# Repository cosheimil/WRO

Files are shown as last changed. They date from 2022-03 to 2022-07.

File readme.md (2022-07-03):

WRO logo
# WRO FE 2022
## Задача:
Задача сезона не просто создание беспилотного автомобиля – это гонка на время. На
трассе не будет одновременно нескольких автомобилей. Вместо этого автомобиль за
попытку должен достичь лучшего времени, проехав несколько кругов полностью
автономно. Дорожные знаки указывают сторону полосы движения, по которой должен
следовать автомобиль. Если на пути красный столб – автомобиль должен держаться
правой стороны полосы, если зеленый - левой стороны полосы.
Задание считается выполненным, если автомобиль проехал 3 круга. Запрещено сбивать
или сдвигать с места дорожные знаки.
Направление, в котором автомобиль должен двигаться по трассе (по часовой стрелке
или против часовой стрелки), будет варьироваться в разных матчах. Стартовая позиция
автомобиля, а также количество и расположение дорожных знаков определяются
случайным образом во время жеребьевки перед матчем (после карантинного времени).
Основа робота - камера OpenMV H7 Plus. С помощью ее и micropython на борту возможно отслеживание объектов внутри кадра и управление пинами GPIO. Так как эта камера фактически pyboard, но с камерой. A pyboard это оффициальная плата с GPIO выводами.
Также выполнен шилд расширения для данной платы на микросхеме drv8833 для управления мотором задней оси и стабилизацией питания на 5в для пиатния камеры.
| Фото | Вид |
| :--- | :--- |
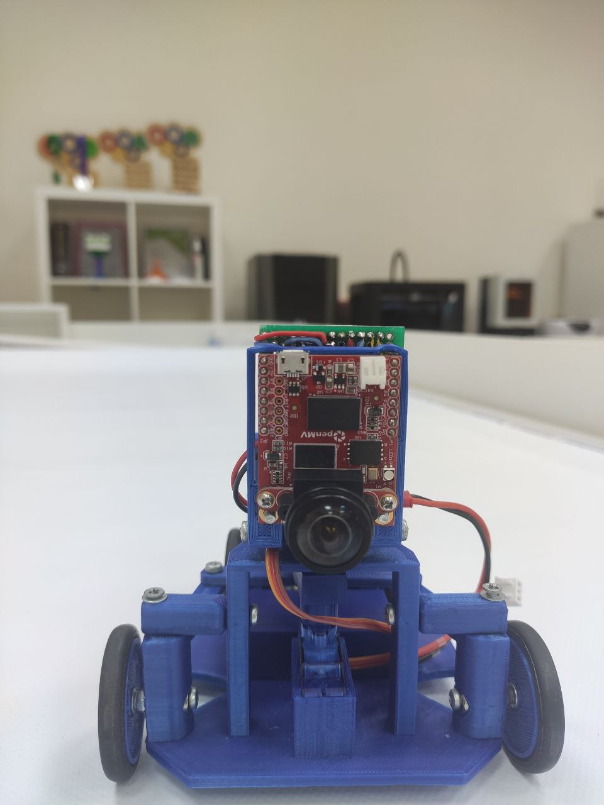
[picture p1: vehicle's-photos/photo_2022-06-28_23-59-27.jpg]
robot1
| | Спереди |
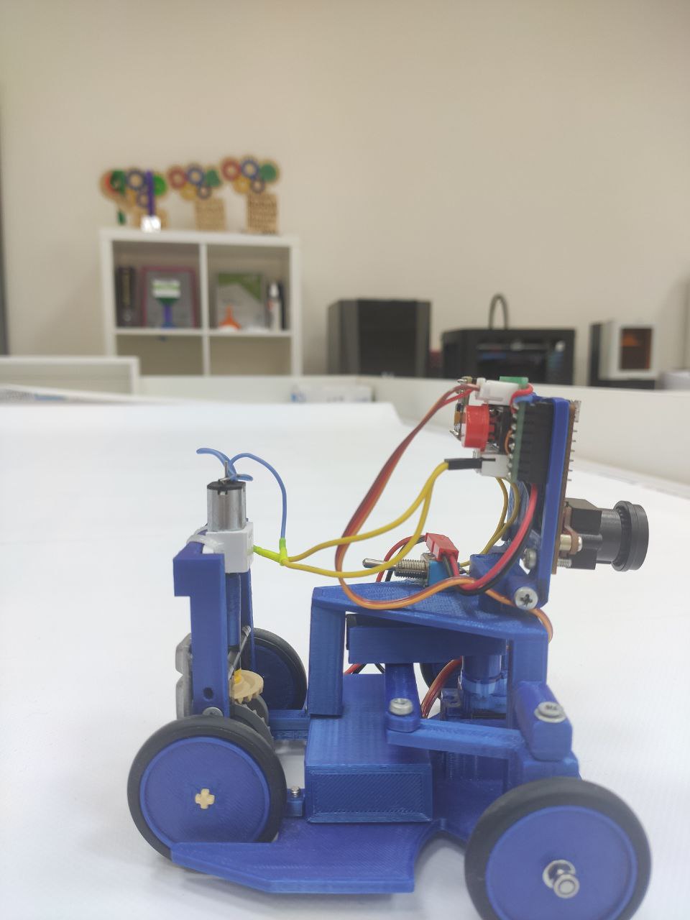
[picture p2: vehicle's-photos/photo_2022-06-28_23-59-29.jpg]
robot2
| | Сбоку |
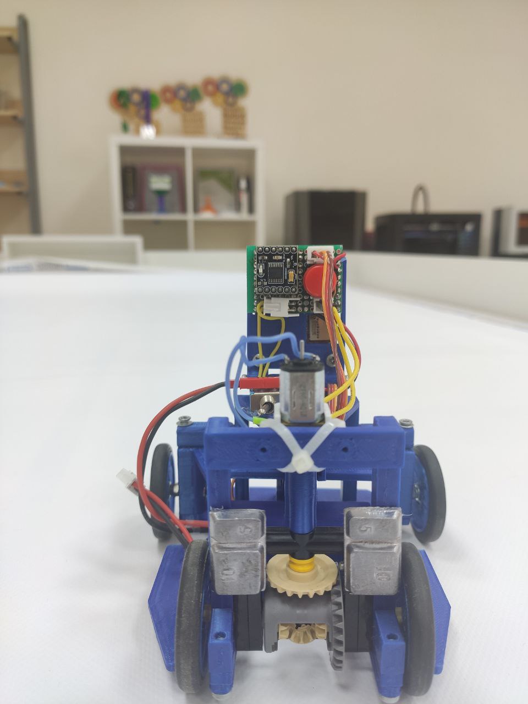
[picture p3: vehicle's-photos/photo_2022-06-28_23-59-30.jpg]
robot3
| | Сзади|
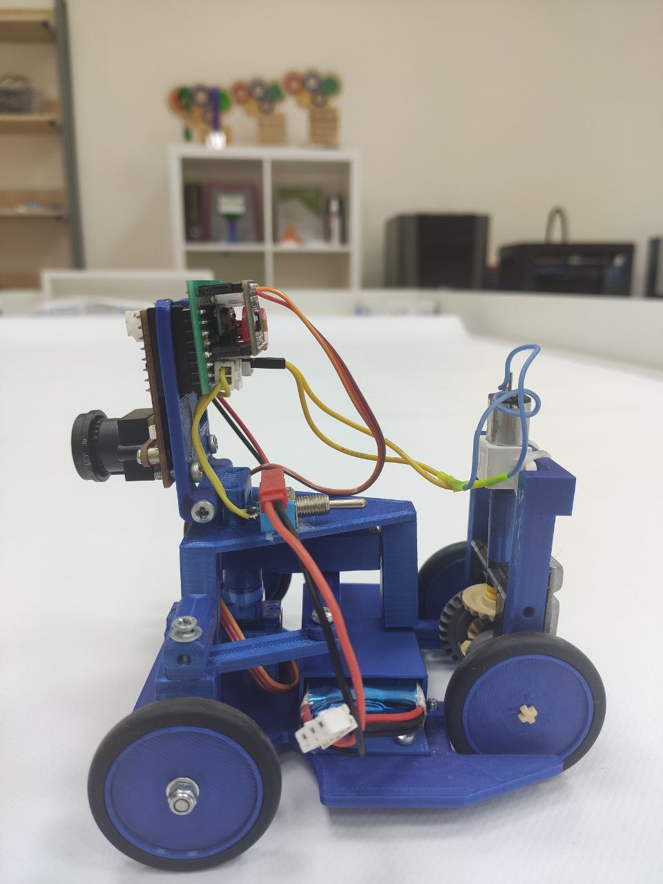
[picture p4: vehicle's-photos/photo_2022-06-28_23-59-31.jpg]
robot4
| | Сбоку|
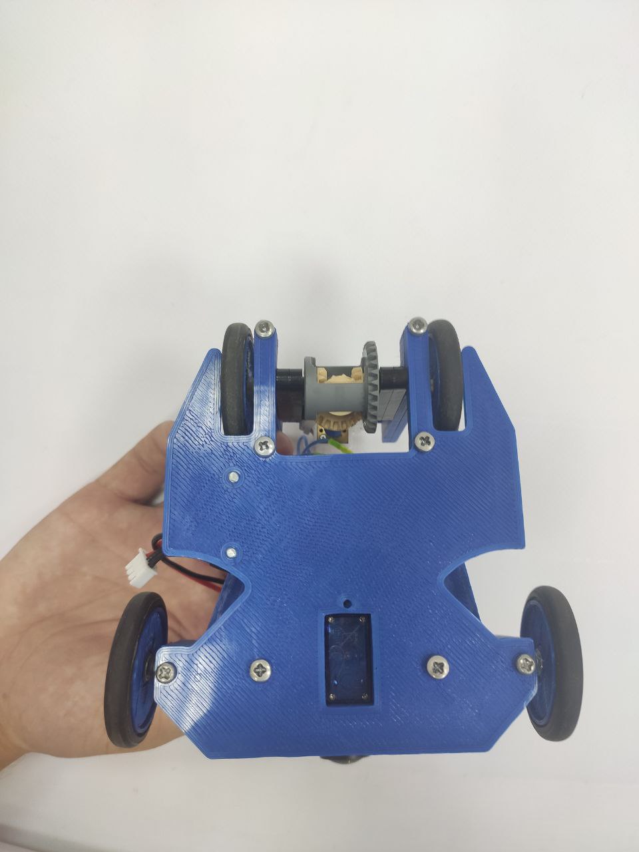
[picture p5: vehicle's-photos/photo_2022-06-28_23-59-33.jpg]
robot5
| | Снизу|
### Конструкция: 
Управление роботом также, как и в настоящей машине: один мотор, передняя ось с соблюдением угла аккермана. Управление передней оси осуществляется с помощью сервопривода MG 90S. А задняя ось приводится в движение с помощью обычного коллекторного мотора с соотношением 150:1 на 6в.
### Реализация конструкции: 
Все части робота были выполнены в CAD Компас 3D V19. в данном CADе присутствуют осовные операции для моделирования и сборка элементов, что идеально подходит для данной задачи.
Все детали напечатаны на 3d-принтере пластиком PLA. Данный пластик идеально подходит для поставленной ранее задачи, так как обладает хорошей прочностью и легким весом.
### Программная часть: 
Камера программируется на MicroPython в среде от производителя - OpenMV IDE. 
В данной среде возможно программировать, отлаживать и загружать код на плату. Также в данной среде поддерживается подсветка синтаксиса и документация к функциям, что делает программирование данной платы очень удобным.

### Алгоритм: 
Алгоритм делится на 3 части:
1) Движение робота до 1 поворота (до первой оранжевой или синей линии на повороте)
2) Движение, если виден кубик
3) Движение при кубике вне кадра

#### 1 
Кадр делится на 2 равные части (разрез по вертикали), определяется кол-во черного в правой и левой. Робот поворачивает в ту сторону, где меньше черного. После того как будет замечена оранжевая или синяя линия (по определенному цветовому диапозону находится прямоугольник некоторого размера) алгоритм переходит ко 2 или 3 части в зависимости от ситуации

#### 2
На некотором расстояние определяется кубик одного из цветов. В зависимости от цвета совершается такой поворот робота (стоит ПИД-регулятор), чтобы центр определенного кубика находился на 20 пикселя от правого (зеленый куб) или от левого (красный куб) края кадра. В таком случае поворот получается достаточно плавным, чтобы не врезаться в куб или стенку

#### 3
Если куба в кадре нет, то робот будет действовать так:
Определяет кол-во черного цвета в правой (если движение против часовой) или в левой (если движение по часовой) половине кадра. Направление движения робота (против часовой или по часовой) определяется по первой увиденной линии на 1 повороте (если оранжевая, то по часовой, если синяя - против часовой). Далее робот с помощью ПИД-регулятора стремится сохранять определенное подобранное кол-во черного в этом секторе.

Тормозит робот после прохождения 12 поворотов (3 круга)

### Процесс сборки
Для сборки робота необходимо напечатать на 3d принтере все компоненты из папки models. И также докупить компоненты [motor](https://www.pololu.com/product/3042), [servo](https://aliexpress.ru/item/1005002235406689.html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,searchweb201602_,searchweb201603_), [motor driver](https://mcustore.ru/store/moduli/drajver-dvigatelya-drv8833/), [OpenMV H7 Plus](https://amperka.ru/product/openmv-cam-h7-plus)
В итоге пакет деталей должен выглядеть примерно так:
- `основа робота`
- `передние кулаки` x2
- `держатели передних кулаков` x2
- `основа камеры`
- `крепление камеры`
- `бампер камеры`
- `батарейный отсек`
- `крепление для дифференциала`
- `колеса` x4
- `вал переходник`
- `OpenMV H7 Plus`
- `сервопривод MG 90S`
- `качалка от сервы`
- `качалка на 3d-принтере`
- `аккамулятор`
- `лего детали`
- `мотор`
- `горстка винтов, гаек и шайб`

1) В основу робота надо вкрутить два передних кулака с использованием шайб m3 и винтов такого же размера
2) В основу необходимо вставить сервопривод и надежно его закрепить внутри самой платформы
3) На сервопривод необходимо одеть качалку с откусанными лепестками и поверх данной конструкции саму качалку, напечатанную на 3d принетере
4) Скрепляется рычаг с кулаки передней оси и продевается в углубление качалки из 3-его шага
5) В основу камеры вкручивается держатель для камеры
6) На камеру одевается бампер
7) Система из шага 6 и 5 скручивается винтами m3 
8) Конструкция из шага 7 вкручивается в основу винтами m3 
9) Батарейный отсек, внутри которой уже заложен аккум, вкручивается в платформу
10) В крепление дифференциала вкручивается сам лего дифференциал
11) Сборка из шага 10 закручивается в платформу
12) На камеру одевается шилд, спаянный по схеме
13) Все провода подключаеются согласно схеме

## Электронные компоненты
#### OpenMV H7 Plus
Мы решили использовать именно эту камеру, так как она обладает хорошим процессором и flash памятью, что позволяет быстрее обрабатывать кадры по сравнению с ее собратьями из данной серии

#### MG 90S
Используется данная серва, потому что алюминиевые шестеренки и алюминиевый вал не дают прокрутится валу и обеспечивает точное позиционирование робота в пространстве

#### pololu motor 6v 150:1
Данный мотор, потому что именно он смог работать адекватно на 7.4v вместо заявленных 6v и не перегреваться

#### преобразователь питания
Использовался китаец под кодовым названием 0j10393, так как за свою цену и размеры он работает идеально

#### DRV8833
Для управления двигателями используется драйвер DRV8833, который позволяет одновременно управлять двумя коллекторными двигателями. Внутри микросхемы драйвера содержится два независимых Н-моста, рассчитанных на напряжение от 2,7 до 10,8 В, с рабочим током каждого канала до 0,5 А без радиатора или до 1,5 А с радиатором, установленным на микросхеме.

## Content
- `models` в этой папке хранятся все файлы робота, напечатанные на 3d-принтере. Все файлы моделей робота, не включая конечную сборку.
- `schemes` содержит принципиальные схемы робота
- `src` вся програмная часть
- `team-photos` фото команды (оффициальное и в процессе работы)
- `vehicle's-photos` фото робота (с разных видов)

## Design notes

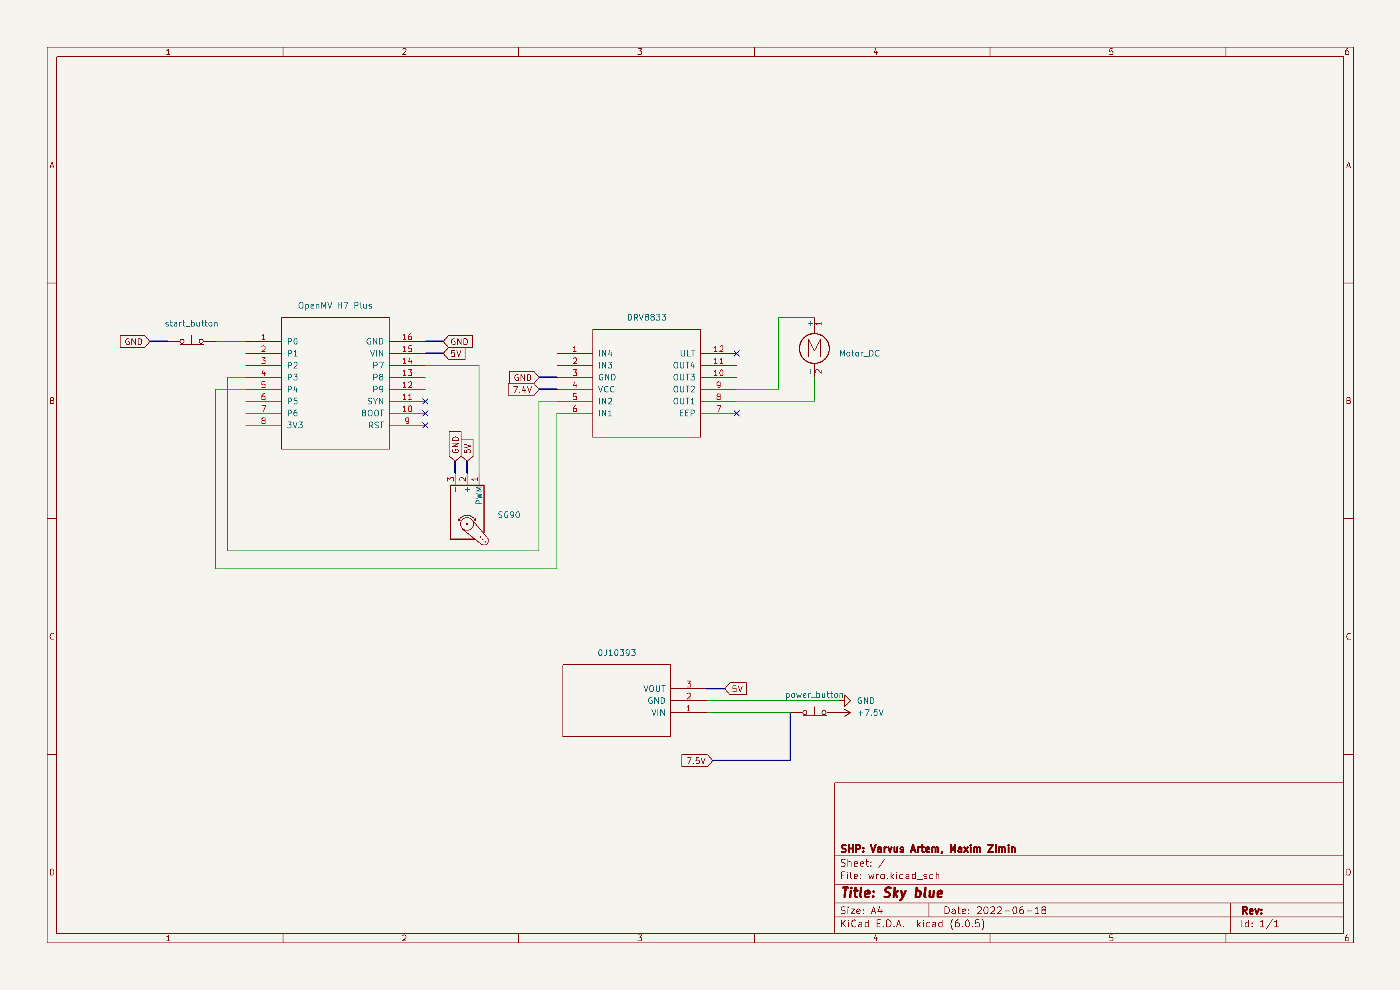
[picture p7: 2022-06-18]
schemes/wro-sheet.png

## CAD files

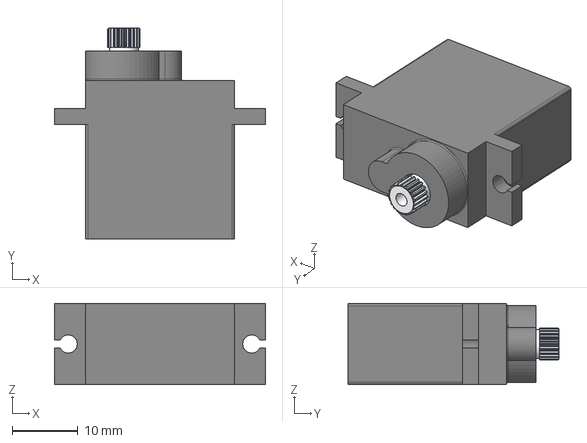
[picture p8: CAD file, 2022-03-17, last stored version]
MG90S Servo Motor.stp
32.2 x 32.2 x 12.4 mm

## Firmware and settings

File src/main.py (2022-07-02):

import time
import math
import sensor
# import image now is unused
import pyb
import utime

# загружаем настройки


# ROI = Rectangle Of Interest (x, y, width, height)
# Левый и правый сектор определяют, в какой части изображания ищутся стенки
# Можешь менять, но они должны быть одинаковые по площади (width * height)
# Размеры полного изображения - 80 * 60 (width * height)
# LINESROI - для нахождения линий на полу (не зависит от LEFTROI и RIGHTROI)
LEFTROI = (0, 0, 60, 120)
RIGHTROI = (100, 0, 60, 120)
LINESROI = (0, 20, 160, 100)
CUBESROI = (0, 0, 160, 120)

LEFTROI_TEST = (0, 50, 40, 60)  # 120 * 160
RIGHTROI_TEST = (80, 50, 40, 60)

# Для определения цветов
# Если тут проблемы, то в OpenMV IDE Инструменты => Машинное зрение => Threshold Editor
# Там подбираешь так, чтобы объект нужного цвета был белый, кортеж копируешь сюда
thresholds = [(0, 19, -128, 127, -128, 127)]  # Черные стенки
# thresholds_blue_line = []  # Синий цвет
# 2 54 -6 52 -128 -5
thresholds_blue_line = [(2, 54, -6, 52, -128, -5)]
thresholds_orange_line = [(19, 58, 9, 64, 1, 76)]


thresholds_green_cube = [(15, 70, -83, -15, 13, 74)]  # цвет зеленого кубика
#thresholds_green_cube1 = [(18, 54, -66, -18, 13, 55)]
#thresholds_green_cube2 = [(17, 49, -79, -15, 14, 74)]
#thresholds_green_cube3 = [(26, 70, -79, -15, 14, 73)]
#thresholds_green_cube4 = [(15, 68, -83, -15, 14, 73)]

thresholds_red_cube = [(0, 53, 5, 70, 12, 54)]  # цвет красного кубика
#thresholds_red_cube1 = [(0, 53, 5, 63, 11, 41)]
#thresholds_red_cube2 = [(9, 43, 12, 69, -22, 54)]
#thresholds_red_cube3 = [(0, 46, 6, 68, 2, 42)]
#thresholds_red_cube4 = [(0, 53, 5, 63, -2, 37)]

thresholds_red_test = [(0, 24, 12, 68, -30, 81)]

MAX_SPEED = 50
MIN_SPEED = 100
CUBE_SPEED = 55

# Максимально маленькое delay
DELAY = 1  # Время торможения и ускорения в секундах

# Угол, при котором он едет прямо (под нашего настрой)
ZERO_ANGLE = 30

# Угол, на который он будет поворачивать направо/налево при виде линий
# Для нашего робота может быть что-то другое, но важно, что
# ZERO_ANGLE - RIGHT_ANGLE  = ZERO_ANGLE - LEFT_ANGLE
RIGHT_ANGLE = 0
LEFT_ANGLE = 60

# Максимальный (по модулю) угол отклонения колес от оси, при котороый
# он едет прямо (под нашего настрой)
MAX_ANGLE = 30

pix_thr = 50
area_thr = 50
CRIT_AREA = 450
NORMAL_WEIGHT = 400

DEBUG = 1

sensor.reset()
sensor.set_pixformat(sensor.RGB565)
sensor.set_framesize(sensor.QQVGA)  # 80 * 60 / 160 * 120
sensor.skip_frames(time=2000)
sensor.set_auto_gain(False, 3.52183)
sensor.set_auto_whitebal(False, rgb_gain_db=(61.4454, 60.2071, 64.5892))
sensor.set_auto_exposure(False, 10124)
sensor.set_vflip(True)
sensor.set_hmirror(True)
clock = time.clock()

pinADir0 = pyb.Pin('P4', pyb.Pin.OUT_PP, pyb.Pin.PULL_NONE)
pinADir1 = pyb.Pin('P3', pyb.Pin.OUT_PP, pyb.Pin.PULL_NONE)
pinADir1.value(1)
tim = pyb.Timer(2, freq=1000)
chA = tim.channel(3, pyb.Timer.PWM, pin=pyb.Pin("P4"))
servo = pyb.Servo(1)
button = pyb.Pin('P1', pyb.Pin.IN, pyb.Pin.PULL_NONE)

servo.angle(ZERO_ANGLE)
chA.pulse_width_percent(MIN_SPEED)


def start_moving():
    # Плавный старт
    for c_speed in range(MIN_SPEED, MAX_SPEED, -10):
        chA.pulse_width_percent(c_speed)
        utime.sleep(DELAY / ((MAX_SPEED - MIN_SPEED) / 10))


def stop_moving():
    # Плавная остановка
    for c_speed in range(MAX_SPEED, MIN_SPEED, 10):
        chA.pulse_width_percent(c_speed)
        utime.sleep(DELAY / ((MAX_SPEED - MIN_SPEED) / 10))


def find_cube(roi, c_thresholds):
    # Поиск кубов нужного цвета в roi
    cubes = img.find_blobs(c_thresholds, roi=roi, pixels_threshold=pix_thr, area_threshold=area_thr)
    if len(cubes) != 0:
        big_cube = cubes[0]
        s = 0
        for c in cubes:
            s += c.pixels()
            if c.pixels() > big_cube.pixels():
                big_cube = c
        return big_cube, s
    else:
        return 0, 0


def find_blobs_weight(img, roi):
    """Для определения самого большого видимого блоба в этой части"""
    # Находятся все блобы в секторе и выбирается самый большой по площади
    # Возвращает кол-во черных пикселей и сам объект
    blobs = img.find_blobs(thresholds, roi=roi, pixels_threshold=250, area_threshold=250)  # 200 200
    s = 0
    for i in blobs:
        s += i.pixels()
        draw_blob(i, img)
    return s


if DEBUG:
    def draw_blob(blob, img):
        """drawing blobs"""
        if blob:
            if blob.elongation() > 0.5:
                img.draw_edges(blob.min_corners(), color=(255, 0, 0))
                img.draw_line(blob.major_axis_line(), color=(0, 255, 0))
                img.draw_line(blob.minor_axis_line(), color=(0, 0, 255))
            img.draw_rectangle(blob.rect())
            img.draw_cross(blob.cx(), blob.cy())
            img.draw_keypoints([(blob.cx(), blob.cy(), int(math.degrees(blob.rotation())))], size=20)

else:
    def draw_blob(blob, img):
        pass

# consts for work
FLAG = ""
LASTFLAG = ""
CORNER_COUNT = 0

# while button.value() == 0:
# pass

start_moving()

pid_red_cube = [0.25, 0.5, 0]  # 0.4 0.5 0
p_dx = 0
ROTATE = ''

t = pyb.millis()

while True:
    clock.tick()
    blue_lines = []
    orange_lines = []

    # Здесь проверка на кол-во пройденных поворотов
    if CORNER_COUNT == 12:
        t = pyb.millis()
    if CORNER_COUNT >= 12:
        # stop_moving()
        # chA.pulse_width_percent(100)
        if pyb.millis() - t > 1000:
            break

    img = sensor.snapshot().lens_corr(1.0, 1.0)

    # Поиск линий
    for blob in img.find_blobs(thresholds_blue_line, pixels_threshold=80, roi=LINESROI,
                               area_threshold=80):
        draw_blob(blob, img)
        # print(blob.rotation_deg())
        blue_lines.append(blob)

    for blob in img.find_blobs(thresholds_orange_line, pixels_threshold=80, roi=LINESROI,
                               area_threshold=80):
        #draw_blob(blob, img)
        orange_lines.append(blob)

    # Определение цвета найденной линии (если нашлась)
    if len(blue_lines) != 0 or len(orange_lines) != 0:
        if len(orange_lines) != 0:
            FLAG = "orange"
            if ROTATE == '':
                ROTATE = 'clockwise'
        elif len(orange_lines) == 0 and len(blue_lines) != 0:
            FLAG = "blue"
            if ROTATE == '':
                ROTATE = 'counter_clockwise'

    green_cube, green_cube_weight = find_cube(CUBESROI, thresholds_green_cube)
    red_cube, red_cube_weight = find_cube(CUBESROI, thresholds_red_cube)


    # На время квалов

    if red_cube:
        print(red_cube.cx())
        print('red:', red_cube.pixels())
    if green_cube:
        print('green:', green_cube.pixels())
        print(green_cube.cx())
    if red_cube_weight != 0 and red_cube.cx() > 30 and red_cube.pixels() >= CRIT_AREA:
        print('yes red:', red_cube.cx())
        print('yes red:', red_cube.pixels())
        #debug
        draw_blob(red_cube, img)
        #debug
        cube_x = red_cube.cx()
        if red_cube.pixels() >= CRIT_AREA:
            dx = CUBESROI[2] - cube_x
            angle = ZERO_ANGLE - (pid_red_cube[0] * dx + pid_red_cube[1] * (dx - p_dx))
            if angle > LEFT_ANGLE:
                angle = LEFT_ANGLE
            elif angle < RIGHT_ANGLE:
                angle = RIGHT_ANGLE
            servo.angle(angle)
        chA.pulse_width_percent(CUBE_SPEED)

    elif green_cube_weight != 0 and green_cube.cx() < 130 and green_cube.pixels() >= CRIT_AREA:
        print('yes green:', green_cube.cx())
        print('yes green:', green_cube.pixels())

        # debug
        draw_blob(green_cube, img)
        # debug
        if green_cube.pixels() >= CRIT_AREA:
            cube_x = green_cube.cx()
            dx = CUBESROI[2] - cube_x
            angle = ZERO_ANGLE + (pid_red_cube[0] * dx + pid_red_cube[1] * (dx - p_dx))
            if angle > LEFT_ANGLE:
                angle = LEFT_ANGLE
            elif angle < RIGHT_ANGLE:
                angle = RIGHT_ANGLE
            servo.angle(angle)
            chA.pulse_width_percent(CUBE_SPEED)

    elif len(img.find_blobs(thresholds, pixels_threshold=250, area_threshold=250)) != 0:
        print('внутри определения')
        left_blob_weight = find_blobs_weight(img, LEFTROI)
        right_blob_weight = find_blobs_weight(img, RIGHTROI)
        if ROTATE == '':

            print('right_blob_weight', right_blob_weight)
            print('left_blob_weight', left_blob_weight)

            dif = left_blob_weight - right_blob_weight
            print(dif)
            dif_percent = dif / (LEFTROI[2] * LEFTROI[3]) * 3
            dif_percent = max(dif_percent, -1)
            dif_percent = min(dif_percent, 1)
            servo.angle(-dif_percent * MAX_ANGLE + ZERO_ANGLE)
            chA.pulse_width_percent(MAX_SPEED)
        elif ROTATE == 'clockwise':

            if right_blob_weight >= 2300:
                left_blob_weight -= 550
            # Поменять на / 400 на финале (?)
            servo.angle(-MAX_ANGLE * (left_blob_weight - 880) / 1100 + ZERO_ANGLE)

            print("left_blob_weight:", left_blob_weight)

            chA.pulse_width_percent(MAX_SPEED)

        elif ROTATE == 'counter_clockwise':
            if left_blob_weight >= 2300:
                right_blob_weight -= 550

            # Поменять на /400 на финале (?)
            servo.angle(MAX_ANGLE * (right_blob_weight - 880) / 1100 + ZERO_ANGLE)

            print("right_blob_weight:", right_blob_weight)

            chA.pulse_width_percent(MAX_SPEED)
    else:
        chA.pulse_width_percent(MAX_SPEED)

    # Подсчет кол-ва пройденных поворотов (прохождение каждой линии - половина поворота)
    if LASTFLAG != FLAG:
        LASTFLAG = FLAG
        CORNER_COUNT += 0.5

    if green_cube_weight == 0 and red_cube_weight == 0:
        p_dx = 0

    # img.binary(thresholds_red_cube)
    # img.erode(2)
    # img.dilate(2)
    # img.binary(thresholds_red_test)
stop_moving()

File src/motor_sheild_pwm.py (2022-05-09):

"""Motor Shield PWM Example"""
#
# This example shows off how to control the motor shield on your
# OpenMV Cam. The motor shield is controlled by using the PYB module
# which lets you do PWM to control the speed and set digital I/O pin
# states. The motor shield needs 6 I/O pins for both motors.

import pyb

# These pins control our direction while the other PWN pins
# below control the speed. The direction for each motor
# is set by an H-Bridge where A0/1 are the two sides of
# one H-Bridge driver. B0/1 are another H-Bridge.
pinADir0 = pyb.Pin("P4", pyb.Pin.OUT_PP, pyb.Pin.PULL_NONE)
pinADir1 = pyb.Pin("P5", pyb.Pin.OUT_PP, pyb.Pin.PULL_NONE)
# pinBDir0 = pyb.Pin('P1', pyb.Pin.OUT_PP, pyb.Pin.PULL_NONE)
# pinBDir1 = pyb.Pin('P0', pyb.Pin.OUT_PP, pyb.Pin.PULL_NONE)

# Dir0/1 must be not equal to each other for forward or backwards
# operation. If they are equal then that's a brake operation.
# If they are not equal then the motor will spin one way other the
# other depending on it's hookup and the value of dir 0.
# pinADir0.value(0)
pinADir0.value(1)

# Dir0/1 must be not equal to each other for forward or backwards
# operation. If they are equal then that's a brake operation.
# If they are not equal then the motor will spin one way other the
# other depending on it's hookup and the value of dir 0.
# pinBDir0.value(0)
# pinBDir1.value(1)

# Create a timer object running at 1KHz which which will power the
# PWM output on our OpenMV Cam. Just needs to be created once.
tim = pyb.Timer(2, freq=1000)

# Use the timer object to create two PWM outputs on the OpenMV Cam.
# These timers control the speed of the motors. You will be setting
# the PWM percentage of these timers repeatedly in your loop.
chA = tim.channel(4, pyb.Timer.PWM, pin=pyb.Pin("P5"))
# chB = tim.channel(2, pyb.Timer.PWM, pin=pyb.Pin("P5"))
servo = pyb.Servo(2)
servo.angle(90, 500)

while True:
    # for i in range(100):
    # pyb.delay(100)
    # chA.pulse_width_percent(99 - i)
    chA.pulse_width_percent(70)

    # for i in range(100):
    # pyb.delay(100)
    # chA.pulse_width_percent(99-i)
    # chB.pulse_width_percent(i)

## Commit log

2022-02-10 10.02
    что то сделал
2022-02-10 фигулина для... короче поступь
2022-04-14 по готовому роботу
2022-04-14 с готового
2022-05-09 general contorl board
2022-05-09 pin docs
2022-05-09 servo docs
2022-05-09 sensor docs
